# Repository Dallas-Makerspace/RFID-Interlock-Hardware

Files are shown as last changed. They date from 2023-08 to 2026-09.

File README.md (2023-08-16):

# RFID-Interlock-Hardware
Documentation and CAD source files for DMS RFID Interlock hardware

This is somewhat fragmentary documentation on the legacy RFID interlock box hardware (not those used in the woodshop) and a new version mechanically based on industry standard DIN rail components. 

Legacy hardware docs are divided into Legacy A - the prototype demo design used on the autolift and Shark lathe, and Legacy B - a group of unit constructed with parts on hand and slight mechanical variation.

Available CAD drawings only support complex parts.   I'll try and fill in some assembly drawings, possibly scans of hand drawings.

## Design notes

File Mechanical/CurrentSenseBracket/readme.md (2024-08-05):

3D printed and bent sheet metal versions of the current sense switch files.

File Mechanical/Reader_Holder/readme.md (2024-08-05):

RFID Reader holder 3D model and 3D print files

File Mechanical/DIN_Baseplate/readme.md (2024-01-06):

Template pattern for DIN baseplate and RIB current sense switch mounting bracket

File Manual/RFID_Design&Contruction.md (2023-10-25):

Dallas Makerspace RFID Lockout Design and Construction

# 1 Design

## 1.1 Avoided custom board design.

This is a no-production-volume design that will built in small quantites over years. Custom board designs were avoided because:

- They will become obsolete and unsupportable rapidly if extreme care is not taken in component selection, and likely even if that care is taken.
- The size and cost advantage is not great in the small number of large machine applications we have.

## 1.2 Readily Available Commodity Parts

The industrial parts used in this design and more expensive that their board level counterparts, but have longer market lives and available from several sources.

# 2 Fabrication and Construction

## 2.1 Waterjet Cutting Connector Hole

The inside of the box needs to protected from the jet. Even though the jet is scattered, it still contains enough energy to damage the internal powder coat. The rear and sidewall opposite the hinge need to be masked or protected in some way.

We've not tested an approach, but duct tape or an acrylic shield to protect the interior finish may work.

# 3 Versions

At this time there are _roughly_ three versions of Interlock. These are (informally) known as Legacy A, Legacy B, and DIN rail based designs.

The Legacy designs use an Eaton contactor with exposed electrical connections and have a protected high voltage compartment with a plastic cover that protects users from any voltage over 24 VAC.

Legacy A versions have the 5 VDC power supply mounted under the input side of the contactor. Only two seem to exist, one on the Shark Lathe in the Machine Shop and one on the Auto Lift. There are rumors of others.

Four Legacy B versions have been built and will likely end up on the Machine Shop milling machines, the Clausing lathe, and the Kalamazoo cold saw. The main apparent difference of this version is that the 5VDC power supply is mounted on the HV compartment wall.

The schematics of the two versions are similar, but not identical. The two legacy A variants are different as well. The Auto Lift unit has an RGB indicator mounted on it's top.

The DIN rail versions are based on a DIN rail mounted on 9.75" square plate.

# 4 Issues

## 4.1 Ethernet connection

Some Raspberry Pi Ethernet interfaces will not connect to some switches. This happens infrequently and can be resolved by connecting to a different brand or model switch. The cause of this issue has not been researched.

# 5 RFID Reader Identification

There are challenges identifying the RFID reader as the identification reported can vary a lot. Most readers do not seem to include a unique serial number. My hope was that future versions could use more than one reader to control multiple clients, unfortunately connecting multiple identical readers to a Raspberry PI only shows one reader. More study is needed. 

One solution was hoped to be to control reader identification by physical port. This is practical utilizing UDEV rules, but depends on underlying hardware. Raspberry Pi hardware versions may be determined by reading /proc/cpuinfo | Revision

[https://ozzmaker.com/check-raspberry-software-hardware-version-command-line/](https://ozzmaker.com/check-raspberry-software-hardware-version-command-line/)

**Table 1 Raspberry Pi Revision Codes**

| **Model and Pi Revision** | **RAM** | **Hardware Revision Code**** from cpuinfo** |
| --- | --- | --- |
| Model B Revision 1.0 | 256MB | 0002 |
| Model B Revision 1.0 + ECN0001 (no fuses, D14 removed) | 256MB | 0003 |
| Model B Revision 2.0
 Mounting holes | 256MB | 0004
 0005
 0006 |
| Model A
 Mounting holes | 256MB | 0007
 0008
 0009 |
| Model B Revision 2.0
 Mounting holes | 512MB | 000d
 000e
 000f |
| Model B+ | 512MB | 0010 |
| Compute Module | 512MB | 0011 |
| Model A+ | 256MB | 0012 |
| Pi 2 Model B | 1GB | a01041 (Sony, UK)
 a21041 (Embest, China) |
| PiZero | 512MB | 900092(no camera connector)
 900093(camera connector) |
| Pi 3 Model B Rev 1.2 | 1GB | a02082 (Sony, UK)
 a22082 (Embest, China) |
| Pi 3 Model B Plus Rev 1.3 | 1GB | a020d3 |
| PiZero W | 512MB | 9000c1 |
| Raspberry Pi 4 Model B Rev 1.1 | 4GB | c03111 |
|
| |
|
| |
| Data from several online sources and direct collection on devices in hand. |

We will need to add a udev rule that assigns reader(s) to port(s) and does so coarse verification of the connected device in an attempt to insure it's a reader.

Port identification and specification

[https://unix.stackexchange.com/questions/66901/how-to-bind-usb-device-under-a-static-name](https://unix.stackexchange.com/questions/66901/how-to-bind-usb-device-under-a-static-name)

udevadm info --attribute-walk /dev/ttyACM0

you get a screed of output but the salient bits are

KERNEL="video0", SUBSYSTEM="video4linux" and KERNELS="1:1.2.4:1.0".

# 6 RFID Reader I/O Assignment

We need to reliably locate the USB RFID reader. The commodity USB RFID readers are mostly based on the Sycreader chipset by RFID Technology Co., Ltd. The problem is that most are not serialized, and offer many different ID strings.

We also need to differentiate between readers in multi-contactor cases. The main advantage of multi-contactor installations is space savings as the cost savings are small.

Facing the the board edge, Pi 2 and 3 the Ethernet connection is on the left and the USB connections are on the right. The Pi 4 is a mirror image with USB ports in the center column.

Shape1 Shape2 Shape3

RFID reader connections are outlined in red. Pi 4 USB 3.0 connections are shaded in blue.

To retain the top USB slots for other purposes, the bottom USB slots are used on Pi 2 and 3 devices.

On the Pi 4 one column of USB connections is version 2.0, and the other is version 3.0. Facing the Pi 4 board edge, the ethernet connector is on the right, the USB 2.0 connections are on the left (outlined in red) and the USB 3.0 connections (highlighted in blue) are in the middle. On a Pi 4 we will use the USB 2.0 connections for the reader to preserve the USB 3.0 connections for other use.

Regardless, we want to assign card readers device names RFIDx where x is 0-9

We will accomplish this with a udev rules file.

The file must be in the /etc/udev/rules.d directory and should be named "10-local.rules" 

The rules file is maintained on the DMS KeyMaster GitHub.

## 6.1 [How to bind USB device under a static name?](https://unix.stackexchange.com/questions/66901/how-to-bind-usb-device-under-a-static-name)

https://unix.stackexchange.com/questions/66901/how-to-bind-usb-device-under-a-static-name

### 6.1.1 Writing udev rules

[http://www.reactivated.net/writing\_udev\_rules.html](http://www.reactivated.net/writing_udev_rules.html)

udevadm info --attribute-walk /dev/ttyAMA0

finding card reader mounts

ls /dev/input/by-path

# 7 Auto restart scripts

A bug in early code versions caused reads of unauthorized tags to crash the software. An expedient work around was used in the form of a bash script that checked for the presence of the process every second. If the process was not active, it would restart KeyMaster. While this is no longer necessary, it's a useful tool in the event of emergent problems like power blips. The original script did not do useful logging, all that happened was that the restart of keymaster generated a private local log. We are in the process of converting all logging to syslog.

Bash scripts can use syslog with the 'logger' command

logger _Some message to write_

There are several options available, including:

-i Log the process ID in each line

-f Log the contents of a specified file

-n Write to the specified remote syslog server

-p Specify a priority

-t Tag the line with a specified tag

See man 1 logger for more information on the tool.

# 8 Alternate AD lookups

Joshua Freedman wrote a new/much simpler AD lookup

https://discord.com/channels/862552330322182165/862555939159539732/1128763838230175744

adm\_d4rkfly3r@prlxjump02:~$ curl -X GET \

-H "Content-type: application/json" \

-H "Accept: application/json" \

-d '{"username":"d4rkfly3r","group":"3D Printer Basics"}' \

"192.168.203.30:8083/usernameGroupMembership"

{"inGroup":true,"activeMember":true}

Or

curl -X GET \

-H "Content-type: application/json" \

-H "Accept: application/json" \

-d '{"badge":"XXXXXXXXXX","group":"Machine Shop Shark Lathe"}' \

"192.168.203.30:8083/badgeGroupMembership"

| **DO NOT copy and paste text directly from this document.**** Word inserts non-printing characters that are not reliably stripped.** |
| --- |

How to use with keyfob #/AUTH GROUP Looks pretty straightforward:

[https://github.com/Dallas-Makerspace/CommonApi/tree/master](https://github.com/Dallas-Makerspace/CommonApi/tree/master)

**Badge in group check**

GET /badgeGroupMembership

Content-Type: application/json

{

"badge": "",

"group": "",

"breakCache": "false"

}

breakCache is optional, and likely should always be left the default false. It is only being left in for debugging purposes. Which will return 200 OK or 417 Expectation failed (when an invalid ldap precondition fails). A 200 OK Body will have a result like below:

# 9 Dust Collector Blast Gate Controls

The blast gates look pretty simple overall, the basically turn into a contact closure. This is true either literally, as in the case of the iVac consumer units, or as a switched AC voltage in the case of more industrial units.

RackMultipart20231024-1-vs8l2p.docx Page 8 of 8[Publish Date]

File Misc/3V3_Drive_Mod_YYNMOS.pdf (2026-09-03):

3/22/2026 | YYNOS 3.3V Drive Mod | OZINDFW

These boards normally require 6 or more volts of drive. The issue is that the optocoupler LED is in series with an LED and a current limiting resistor. The optocoupler voltage drop is about 1.7V at 20 mA. Since the indicator LED is also more than 1.5V, 3.3V drive will not work. The 470 Ohm current limiting resistor would limit drive to the optocoupler to only about 3 mA which is not enough drive for reliable operation.

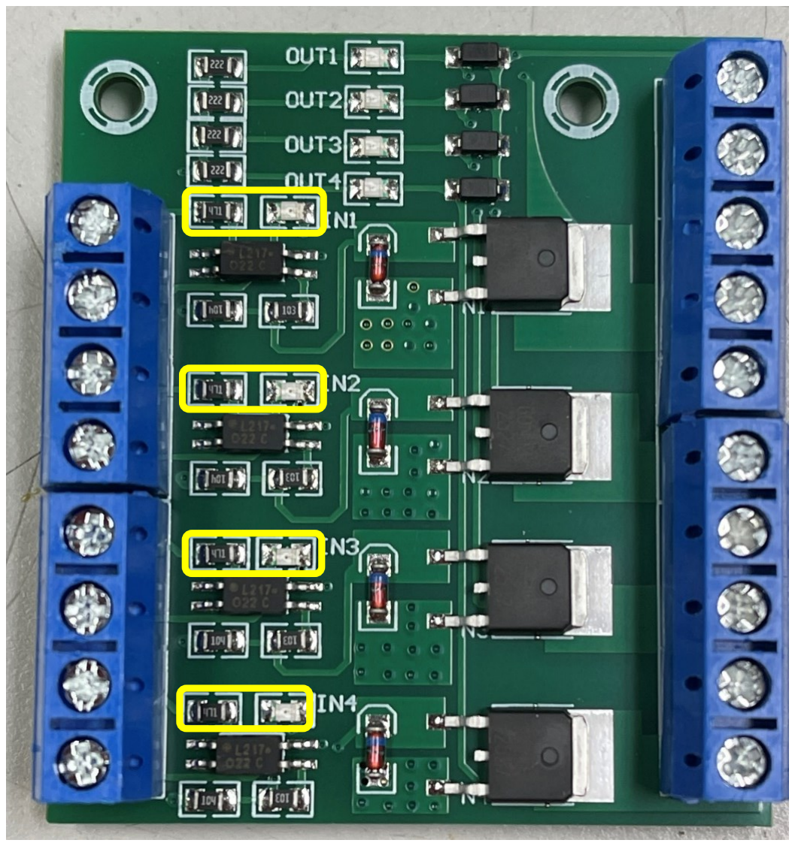
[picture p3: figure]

Figure 1 Unmodified YYNMOS-4

The modification involves removing the LED and replacing it with a short, and replacing the current limiting resistor with a lower value. I used 120 ohms which results in about 15 mA of drive – more than enough.

In Figure 2 I used a 120 ohm 0805 size surface mount resistor and a solder blob short. I didn’t have any zero ohm resistors of the correct physical size. I could have used two resistors that added up to the appropriate value, but I had the 120s on hand.

3/22/2026 | YYNOS 3.3V Drive Mod | OZINDFW

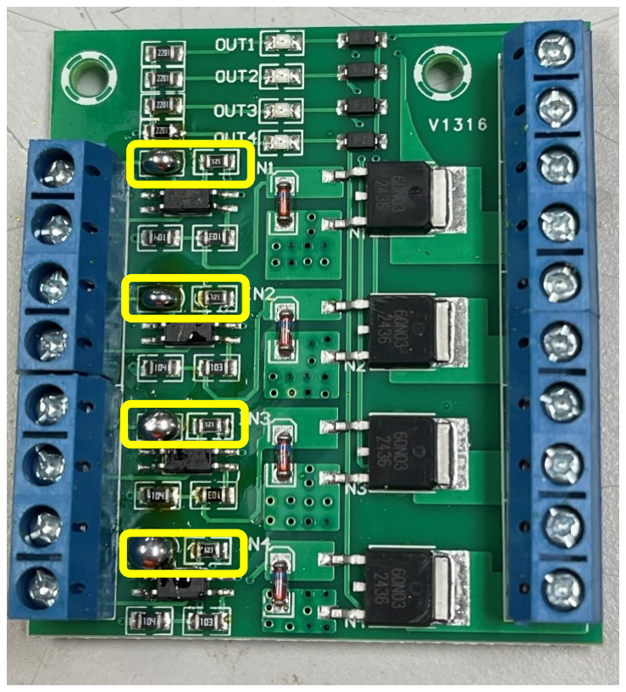
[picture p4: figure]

Figure 2 Modified YYNMOS-4

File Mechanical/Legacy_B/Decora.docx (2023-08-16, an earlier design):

Yes, all "Decora" style devices share the same cover plate opening, within a couple of thousandths of an inch (+/-.005" or so). GFCI receptacles also fit this description, as well as many dimmers, timers and "smart switches".

For instance the opening on a Hubbell plate is 1.312"x2.625" (http://www.hubbellcatalog.com/canada/catalogpages/section-c.pdf), while these Leviton are slightly different, but all within a reasonable spec to be called the same.

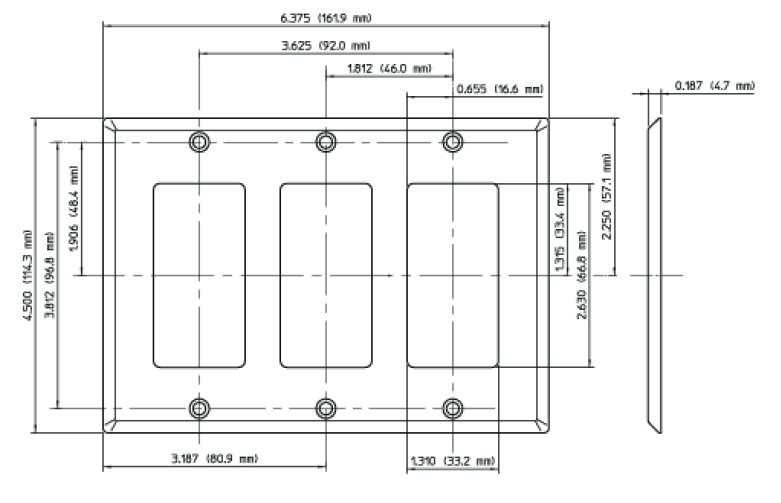
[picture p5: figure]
3 gang Decora cover plate drawing

W: 1.310 (min)

L: 2.630 (min)

R: 0.094 (0.079 347V)

C: 3.812 (4.062 347V) +/- 0.010 (counter-sunk for #6-32 UNC oval head machine screw)

Application (Face of device): 1.300 (max) W x 2.620 (max) L

page iv (https://www.nema.org/Standards/view/Wiring-Devices-Dimensional-Specifications) notes: (#1) dimensions are in inches (#2) tolerances are +/- 0.005 (#10) dimensions are for interchangeability and do not preclude other designs.

NEMA WD 6-2016 (https://www.nema.org/Standards/view/Wiring-Devices-Dimensional-Specifications), page 5 says:

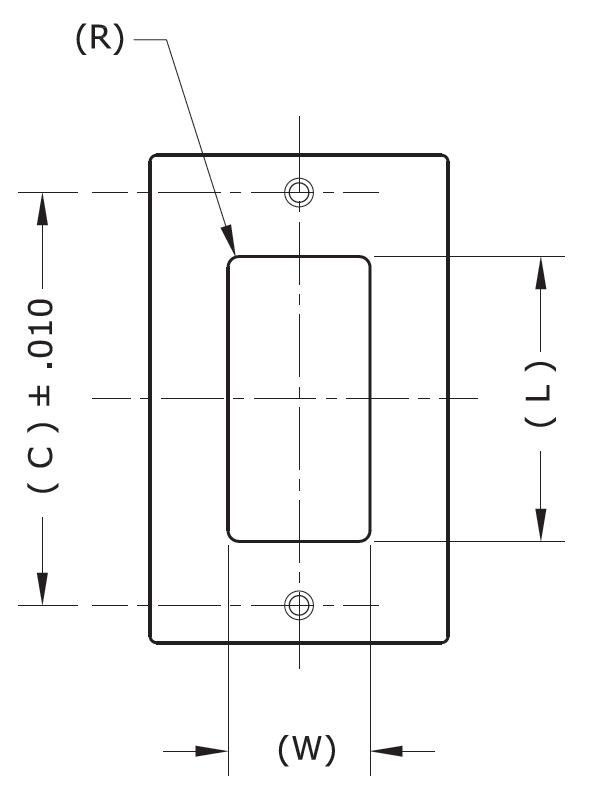
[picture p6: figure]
Wallplate Dimensions for Rectangular Face Devices

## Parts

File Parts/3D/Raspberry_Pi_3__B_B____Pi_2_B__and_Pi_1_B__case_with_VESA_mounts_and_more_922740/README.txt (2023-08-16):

Raspberry Pi 3 (B/B+), Pi 2 B, and Pi 1 B+ case with VESA mounts and more by 0110-M-P on Thingiverse: https://www.thingiverse.com/thing:922740

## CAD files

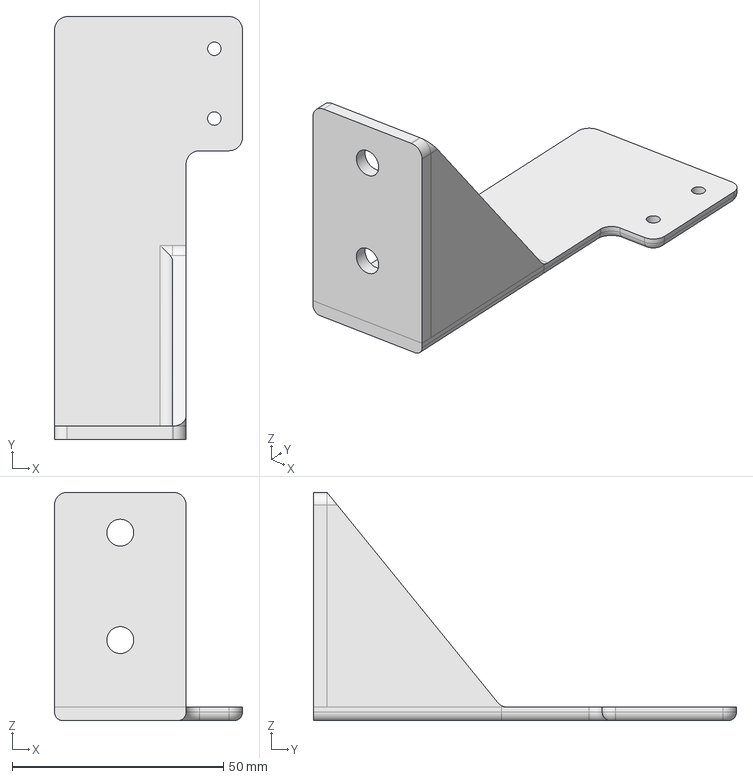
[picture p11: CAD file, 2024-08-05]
Mechanical/CurrentSenseBracket/RFID_CurrentSense_Bracket_3D_0v1d.FCStd
44.5 x 100.0 x 54.0 mm

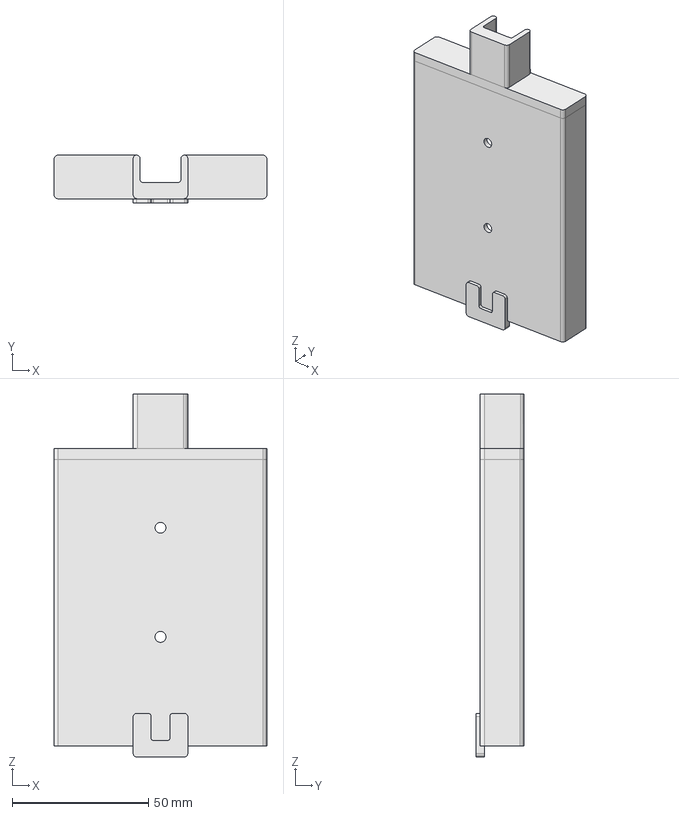
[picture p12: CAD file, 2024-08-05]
Mechanical/Reader_Holder/Reader_Holder_0v6a.FCStd
78.0 x 17.5 x 133.0 mm

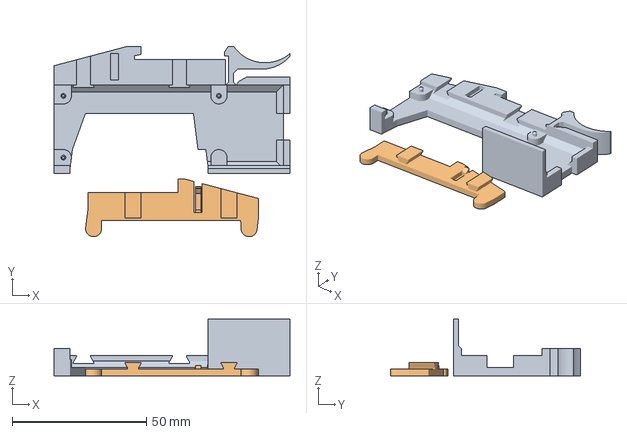
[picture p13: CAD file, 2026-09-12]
Mechanical/RPi_Zero_DIN_Mount/rpi_zero_din_rail.3mf
88.0 x 71.0 x 21.1 mm
rpi_zero_din_rail.stl
stopper.stl

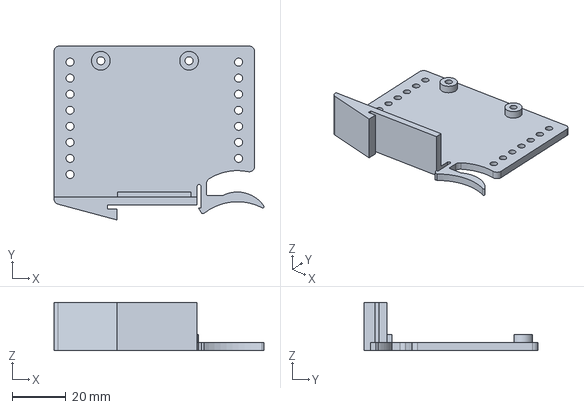
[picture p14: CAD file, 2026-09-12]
Mechanical/YYNMOS-4_MOSFET_Sw_Bracket/YYNMOS4_DIN_0v4.FCStd
78.5 x 65.0 x 18.0 mm

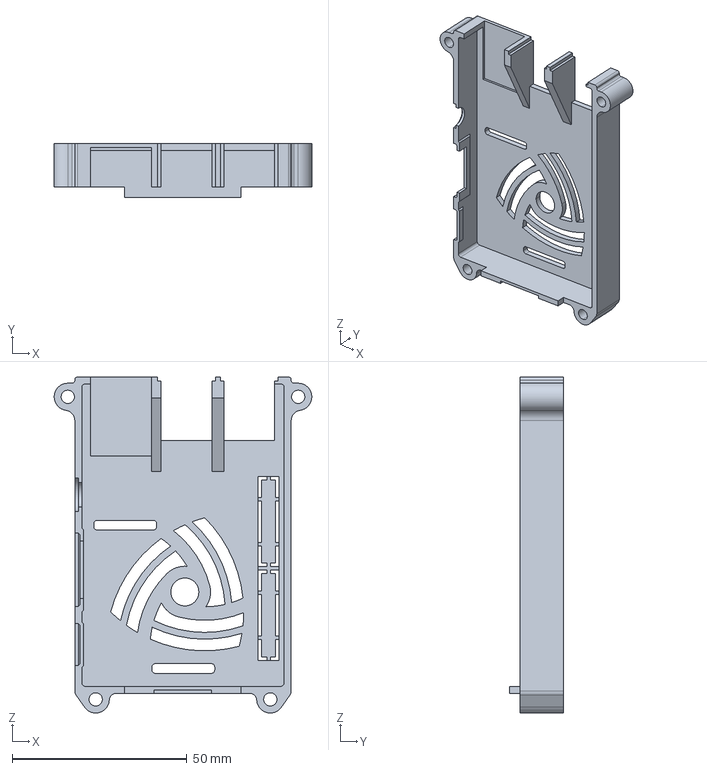
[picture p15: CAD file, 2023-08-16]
Parts/3D/Raspberry_Pi_3__B_B____Pi_2_B__and_Pi_1_B__case_with_VESA_mounts_and_more_922740/files/rpi2-top.stp
73.8 x 15.5 x 96.2 mm

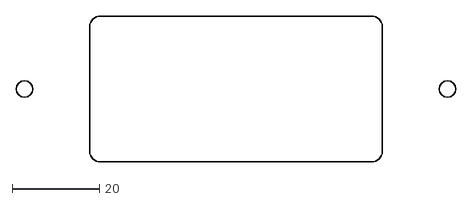
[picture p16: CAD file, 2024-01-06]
Mechanical/KeystoneCutout/KeystoneCutout0v1b.dxf
100.6 x 33.4

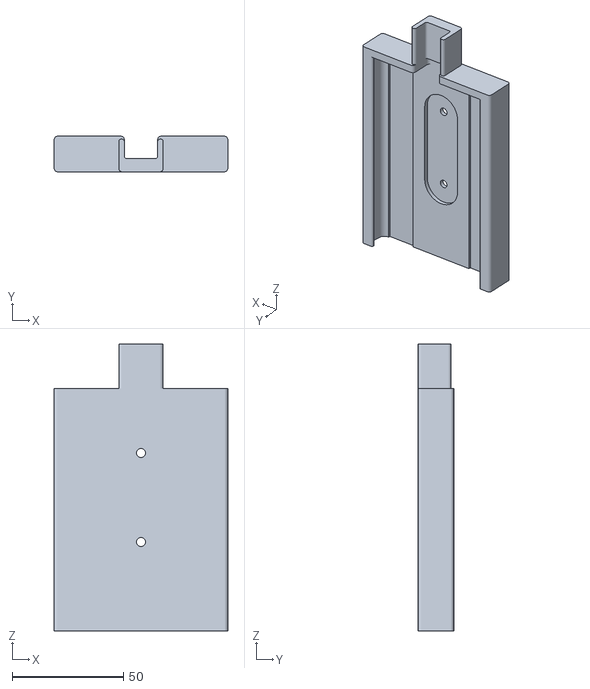
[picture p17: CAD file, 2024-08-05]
Mechanical/Reader_Holder/Reader_Holder_0v6a-Body.stl
78.0 x 16.0 x 129.0

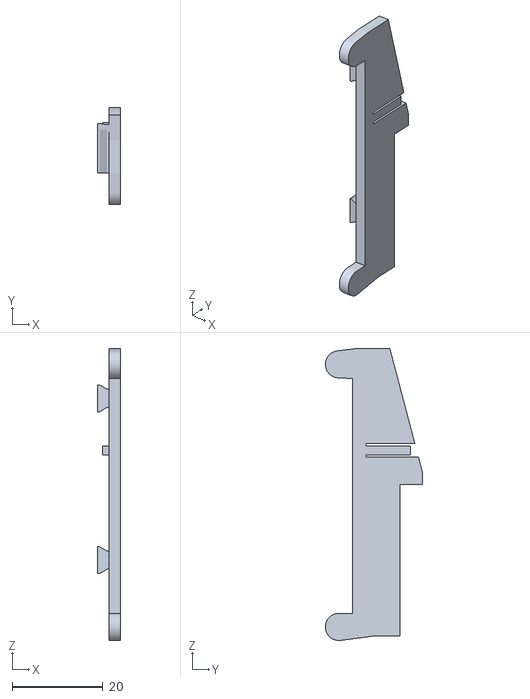
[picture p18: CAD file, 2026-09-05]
Mechanical/RPi_Zero_DIN_Mount/stopper.stl
5.01 x 21.5 x 64.5

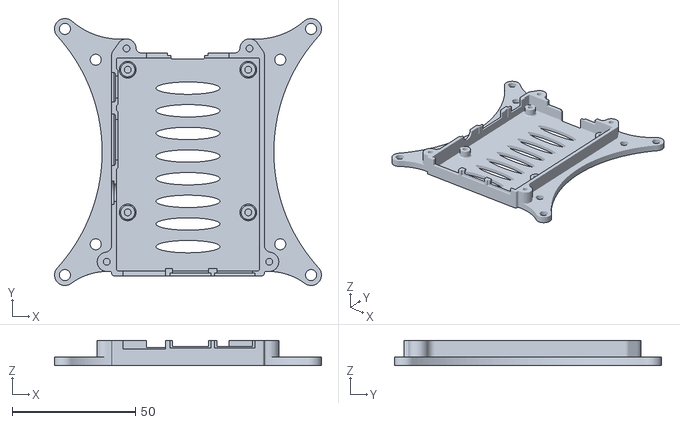
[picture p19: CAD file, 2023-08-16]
Parts/3D/Raspberry_Pi_3__B_B____Pi_2_B__and_Pi_1_B__case_with_VESA_mounts_and_more_922740/files/rpi3-bottom_100mm-vesa_netfabb.stl
108.5 x 108.5 x 10.3

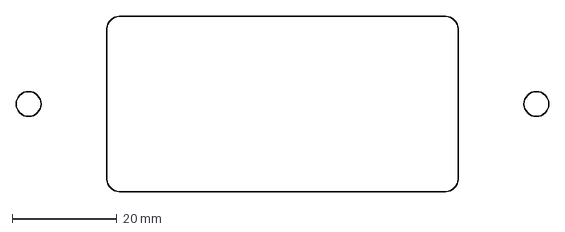
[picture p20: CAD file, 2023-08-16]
Mechanical/KeystoneCutout/KeystoneCutout0v1a.dxf
101.6 x 33.4 mm

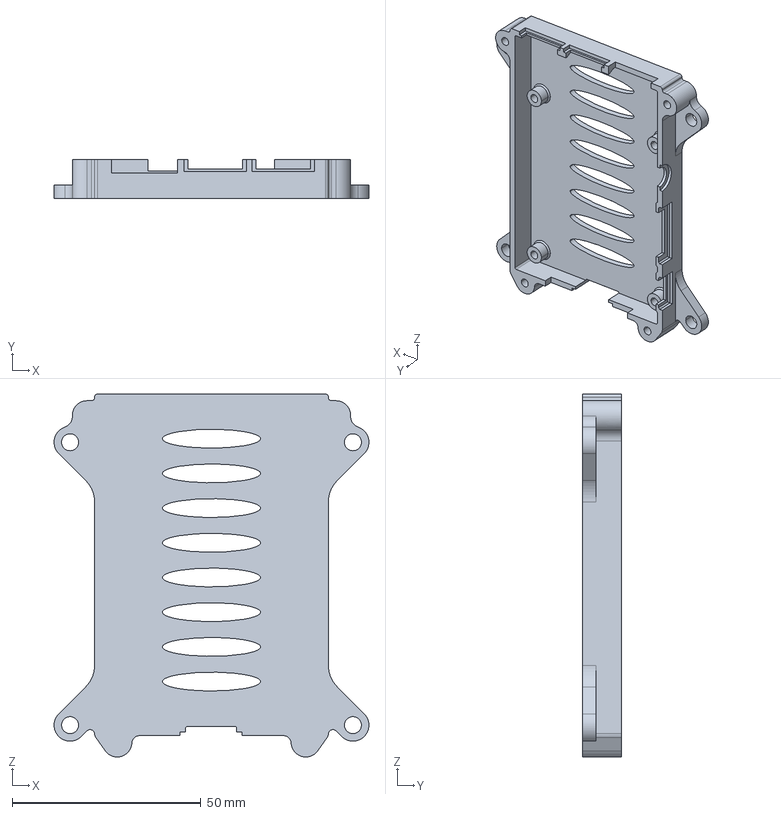
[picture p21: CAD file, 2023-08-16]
Parts/3D/Raspberry_Pi_3__B_B____Pi_2_B__and_Pi_1_B__case_with_VESA_mounts_and_more_922740/files/rpi3-bottom.stp
83.5 x 10.3 x 96.2 mm

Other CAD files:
Mechanical/DIN_Baseplate/RFID_CurrentSense_Bracket_3D_0v1b-Body.stl
Mechanical/KeystoneCutout/KeystoneCutout0v1.FCStd
Mechanical/CurrentSenseBracket/RFID_CurrentSense_Bracket_3D_0v1d-Body.stl
Mechanical/DIN_Baseplate/RFID_CurrentSense_Bracket_3D_0v1b.FCStd
Mechanical/YYNMOS-4_MOSFET_Sw_Bracket/YYNMOS4_DIN_0v3-Case.step
Mechanical/CurrentSenseBracket/RFID_CurrentSense_Bracket_3D_0v1d-BodyFillet.stl
Mechanical/DIN_Baseplate/RFID_CurrentSense_Bracket_Dim_0v2.FCStd
Mechanical/CurrentSenseBracket/RFID_CurrentSense_Bracket_0v2.DXF
Mechanical/CurrentSenseBracket/RFID_CurrentSense_Bracket_0v2.FCStd
Mechanical/CurrentSenseBracket/RFID_CurrentSense_Bracket_sheet_Metal_0v1b.FCStd
Mechanical/DIN_Baseplate/RFID_CurrentSense_Bracket_Bare_0v2.FCStd
Mechanical/DIN_Baseplate/RFID_LO_DIN_Baseplate_0v2b.FCStd
Mechanical/DIN_Baseplate/RFID_LO_DIN_Baseplate_0v2b.dxf
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

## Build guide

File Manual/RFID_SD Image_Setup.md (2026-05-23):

Dallas Makerspace Legacy RFID Lockout SD Card Setup

# 1 Create New SD Card image

## 1.1 Obtain Raspberry Pi OS Image File

Download or otherwise obtain a copy of the latest Raspberry Pi OS (was called Raspbian.) Select the lightest 32-bit version available (no desktop, etc.)

[https://www.raspberrypi.com/software/](https://www.raspberrypi.com/software/)

## 1.2 Card Selection

The best option appears to be "high endurance" SD cards of 8 GB or greater.
These are usually made for security video and other high write duty cycle applications.
 
## 1.3 Raspberry Pi OS Installation

Using the SD card imager of your choice, or the Raspberry Pi foundation Raspberry Pi Imager, install an image on

You can get an image from the Raspberry Pi site that includes a Raspberry pi OS installer, but these have historically been limited to the (large) desktop version.

### 1.3.1 balenaEtcher

Available for Windows, MacOS, and Linux, this is a simple and very effective application.

https://balenaetcher.org/

### 1.3.2 Win32DiskImager

| **Caution!**** There are several sites that purport offer Win32DiskImager downloads that add malware.** |
| --- |

The correct 'official' site is:

[https://sourceforge.net/projects/win32diskimager/files/latest/download](https://sourceforge.net/projects/win32diskimager/files/latest/download)

## 1.4 Network Configuration

Need to modify network manager settings, so edit:

_/etc/dhcpcd.conf_

And set the appropriate static address

Note: Using Network Manager leads to host of issues that make copying the card image a mess. Network Manager includes the ethernet interface mac address in a GUID used a number of places, not all of which appear to be documented.

### 1.4.1 WiFi Configuration

If the applicaiton uses WiFi use the command:

_sudo nmtui_

to configure WiFi and IP settings with the appropriate static address. Some versions of Raspberry Pi OS need options disabled to maintain a reliable connection. If you observe frequent data drops try:

Create a file called /etc/modprobe.d/brcmfmac.conf

 with the following content:

_options brcmfmac roamoff=1 feature_disable=0x82000_

Reference: https://forums.raspberrypi.com/viewtopic.php?t=372254

### 1.4.2  SSHD Configuration

***Note that this step appears to not be needed and breaks Trixie based versions***

The OpenSSH daemon has added QoS metric requirements that the Pi Zero W Wifi can't meet. This results in dropped SSH/SFTP sessions, often before login completes. Edit 

_/etc/ssh/sshd_config_

and add the line

_IPQoS 0x00_

Refernce: https://raspberrypi.stackexchange.com/questions/143142/has-anyone-solved-raspberry-pi-zero-w-ssh-client-loop-send-disconnect-broken

## 1.5 Raspberry Pi OS Configuration

On first boot you will be asked for a language, username and password. Use:

- Select US English
- Username keymaster,
- Password dmsDMS

Run:

**sudo raspi-config**

- Update raspi-config tool to latest version. If you just downloaded the OS, it is likely the tool is the latest version, but this is not guaranteed.

## 1.5 Make raspi-config changes:

*Note that later versions of raspi-config renumber options.*

### 1.5.1 System Options

- 1 System|S4 Hostname Interlock-Test-1
- S5 Boot/Autologin|B2 Console Autologin
- S6 Network at boot (do not wait for network)
- S8 Power LED – change to indicates power if option is available

### 1.5.2 Display Options (none)

### 1.5.3 Interface Options

- I2 SSH (Enable)
- I4 SPI (enable) if PiFace is used (Legacy only)

### 1.5.4 Localization

- L1 Locale EN\_US.UTF-8 (disable EN\_GB if selected) and set en\_US as default
- L2 Timezone America/Chicago
- L3 Keyboard Generic 104-Key/US default layout no compose key
- L4 WLAN Country US (United States)

### 1.5.5 Advanced Options

- A4 Network Interface Names (Disable predictable network I/F Names)
- AA Network Config|dhcpcd

**NOTE: If this image is intended to be copied to other cards, it's best to hold off on the following config until the final card it used.**

The A1 Expand Filesystem option expands the Pi OS image to fill the entire card. This will restrict the use of the image to cards larger than the image

- A1 Expand Filesystem – (hold till complete)

Finish and reboot

## 1.6 Remove avahi

Avahi generates mDNS traffic that adds no value in this application. To remove it:

sudo apt-get purge avahi-daemon

## 1.7 Install Python Libs

Before doing anything else update the OS

_sudo apt-get update_

install pip

_sudo apt-get install python3-pip_

_sudo pip install evdev_

later versions of Rapberry Pi OS 'externally manage' Pi libraries and require anything not upported by the OS to be installed in a virtual environment.  evdv *IS* supported so can be installed with APT:

_sudo apt install python3-evdev_

### 1.7.1 Configure Pi GPIO Support

In order to use the GPIO ports your user must be a member of the gpio group. 
The pi user is a member by default, other users need to be added manually. To add a user:

  sudo usermod -a -G gpio keymaster

### 1.7.2 Piface DigitalIO 2 Support

*PiFace is _ **only** _ used on legacy systems as the PiFace DigitalIO 2 cards are no longer available.*

_pip install pifacecommon_

_pip install pifacedigitalio_

## 1.9 Keymaster Install

Copy Python code and subdirectories into /home/Keymaster

Add and configure KeyMaster.ini file

## 1.8 Install UDEV Rules

Copy the latest version of the UDEV rules file to /etc/udev/rules.d directory. The file should be named "10-local.rules"

## 1.10 Bash Script Edits

The ".bashrc" needs some additions

Copy line(s) from aux\_files\bashrc-addendum.bash into the end of .bashrc

Copy file aux\_files\KeyMaster\_Start.sh to \home\keymaster and make executable with

_sudo chmod +x KeyMaster\_Start.sh_

## 1.12 Read Only Card Configuration

While we have examples of systems running cards with local logging to SD for years, Flash wearout is a well-documented issue. The best option seems to be to log to local RAMDISK and network logger.

Add instructions here.

[1](#sdfootnote1anc) While cards smaller than 8 GiB may fit an image, smaller cards don't really leave enough working room for flash wear leveling.

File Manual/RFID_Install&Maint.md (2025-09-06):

Dallas Makerspace Legacy RFID Lockout Installation and Maintenance
|

| **DO NOT configure for operation at input voltage greater than 240V.** If 480V operation is required, see Appendix A; Configuration for operation on 480 V (Untested) |
| --- |

# 1 Before You Begin

Note that the RFID Interlocks as currently built and tested have not been modified for power in/out ports, any indicators, or an Emergency Stop switch as these are installation dependent.  You will need to survey and plan the installation so that any required chassis modifications can be made prior to installation and commissioning. These instructions do not cover these modifications nor do they discuss mounting the interlock chassis/box.

## 1.1 Material Required

- Interlock hardware for configuration.
- Suitable micro SD card – minimum of 4 GiB, recommend 16 GiB or greater to provide lots of spare capacity for wear leveling.
- Box mounting material (wall anchors, etc.)
- Double sided mounting tape for reader installation.

## 1.2 Required Information

Have the following information at hand:

- Hostname
- Fixed IP address for unit (ping hostname while at DMS to obtain.)
- The Active Directory security group that controls the target device (these are continuously added to and changing, but one example is "Automotive 102 (Lift Training)" for the Automotive Committee car lift.
- The password for the device. Generating the password with and storing it in the DMS Bitwarden IoT folder before using it would be a good idea.
- Required operating voltage
- Phase count (single or three phase)
- Load current or horsepower rating

## 1.3 Tools/Facilities

Have access to:

- SSH/SFTP terminal
- Multimeter
- Test supply of required voltage
- DMS Ethernet port on VLAN 400 (the IoT VLAN)
- Very small screwdrivers required for current switch adjustment and DIN connection block screws
- 1/4" flat blade screwdriver and #1 Phillips screwdriver
- 3/8" socket or nutdriver for installing the baseplate retaining nuts.

# 2 Create and Configure SD card

Copy the latest image on to a micro SD or create one according to the instructions in the latest version of RFID\_LO\_SD\_IMAGE\_Setup

## 2.1 SD configuration

You can do this from the autologin console on the Pi or by SSH to the default image DNS of Interlock-Test-1 with the password dmsDMS. If you use SSH you will need a network connection on VLAN 400.

### 2.1.1 Resize Partition

Run the Raspberry Pi configuration utility and resize the partition to fill the card.

sudo raspi-config

select Advanced Options, and option A1 Expand Filesystem

### 2.1.2 Set hostname

Edit the /etc/hostname file:

sudo nano /etc/hostname

and enter the desired hostname. Edit the /etc/hosts

sudo nano /etc/hosts

file to change the localhost home alias entry (probably the last in the file) from:

127.0.0.1 Interlock-Test-1

To reflect the new hostname.

#### 2.1.2.1 Hostname Selection

Three elements separated by hyphens, all caps.

COMMITTEE-MACHINE-INDEX

**COMMITTEE** name - Wood, Machine, Metal, etc

**MACHINE** name – eg SAWSTOP for SawStop table saw, or COLCHESTER for Colchester lathe

**INDEX** – a sequential number starting with one and continuing with upper case letters if needed

So the woodshop's second SawStop would be WOOD-SAWSTOP-2

## 2.2 Password Setting

Set new passwords for the Keymaster User account in accordance with DMS password selection standards and enter it in Bitwarden in the IoT folder for the hostname.

## 2.3 Keymaster Configuration

Select AD name for authorization. 

Edit the [ADCommonAPIAuth] section of /home/KeyMaster/KeyMaster.ini

[ADCommonAPIAuth]

url = http://192.168.203.30:8083/badgeGroupMembership

group =

(where the authorization group follows the equal sign and is not in quotes)

~~Edit the [ADApiAuth] section of /home/KeyMaster/KeyMaster.ini~~

~~[ADApiAuth]~~

~~url = http://192.168.200.32:8080/api/v1/lookupByRfid~~

~~# Groups denied are checked first, then groups allowed are checked~~

~~groups\_denied =~~

~~groups\_allowed = Automotive 102 (Lift Training)~~

~~and replace the groups\_allowed entry with the AD for the system. groups\_denied should remain blank.~~

## 2.4 Network Configuration

It is probably best to leave this to the very last as interlocks at DMS use fixed IPs on a dedicated VLAN subnet. The VLAN is 400 and is determined by switch port configuration. The subnet is the RFC1918 non-routable, private range 10.0.0.0 0 - 10.255.255.255 (10/8 prefix)

The IoT IP range is not routable by the DMS user subnet.

~~Copy dhcpcd.conf from the aux-files/Network folder to /etc/dhcpcd.conf and edit the static IP address~~

Use Network Manager to configure the netowrk interface:

sudo nmtui

## 2.5 Labelling

- Apply High Voltage Caution label if not present
- Apply hostname label to cabinet (best to use top of cabinet so label is visible with door open
- Apply hostname label to baseplate

# 3 Installation

- Remove ground screw and four mounting nuts on baseplate (need pic) and remove the baseplate assembly.
- Select and remove cable entry and exit knockouts or cut holes for this purpose.
- Mount box/cabinet
- Route input and output cables
- Reinstall Baseplate
- Install (but do not tighten) ground screw.
- Place all corner nuts finger tight, then tighten them completely
- Tighten the ground screw

## 3.1 Wiring

### 3.1.1 Single Phase Application

In single phase applications the neutral should use the contactor middle terminals. The line (hot) should pass through the current sensor.

### 3.1.2 Three Phase Application

# 4 Test and Calibration

## 4.1 Current Sensor adjustment

Turn the machine in it's unloaded running state (with motor on, but unloaded.) Adjust current switch so light just comes on. Turn motor off and verify sensor light turns off.

# 5 Commissioning
- Create and initially populate controlling AD entry (if not already done - need at least one entry for testing.)
- Edit keymaster.ini with new AD (if not already done.)
- Update Password from default and generate Bitwarden entry for interlock.
- Delete existing logs (keymaster and console) to get rid of leagacy image and testing entries
- Reboot and check function.

# 6 Maintenance

Log checks

# Appendix A

# 7 Configuration For Operation On 480 V (Untested)

**NOTE THAT THIS CONFIGURITION IS UNTESTED AND ONLY APPLIES TO LEGACY STYLE INTERLOCKS**

The low voltage power supply input is rated for a maximum input operating voltage of 240 V. It should be possible to use the transformer input as an autoformer. Connect the power supply input between the common and 208V tap. Connect the 480 V input between the common and 480V tap.

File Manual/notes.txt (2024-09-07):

There may be power save issues that cause the wifi to dissappear (device and all)

See https://raspberrypi.stackexchange.com/questions/138688/wifi-disconnects-after-6-hours-on-raspian-11-pi-zero-2w

and   https://raspberrypi.stackexchange.com/questions/96606/make-iw-wlan0-set-power-save-off-permanent

So far I haven't been able to successfully disable it. Except that I have.  It's not clear if 

sudo systemctl disable wifi_powersave@on.service
sudo systemctl enable wifi_powersave@off.service

did this after

One way to accomplish this is to build a systemd unit file which can execute the necessary command at boot. I will give you here a bit more comfortable example for switching off or on power_save. Create a Unit file with:

rpi ~$ sudo systemctl --full --force edit wifi_powersave@.service

In the empty editor insert these statements, save them and quit the editor:

[Unit]
Description=Set WiFi power save %i
After=sys-subsystem-net-devices-wlan0.device

[Service]
Type=oneshot
RemainAfterExit=yes
ExecStart=/sbin/iw dev wlan0 set power_save %i

[Install]
WantedBy=sys-subsystem-net-devices-wlan0.device

editing /etc/rc.local did not seem to work on boot up

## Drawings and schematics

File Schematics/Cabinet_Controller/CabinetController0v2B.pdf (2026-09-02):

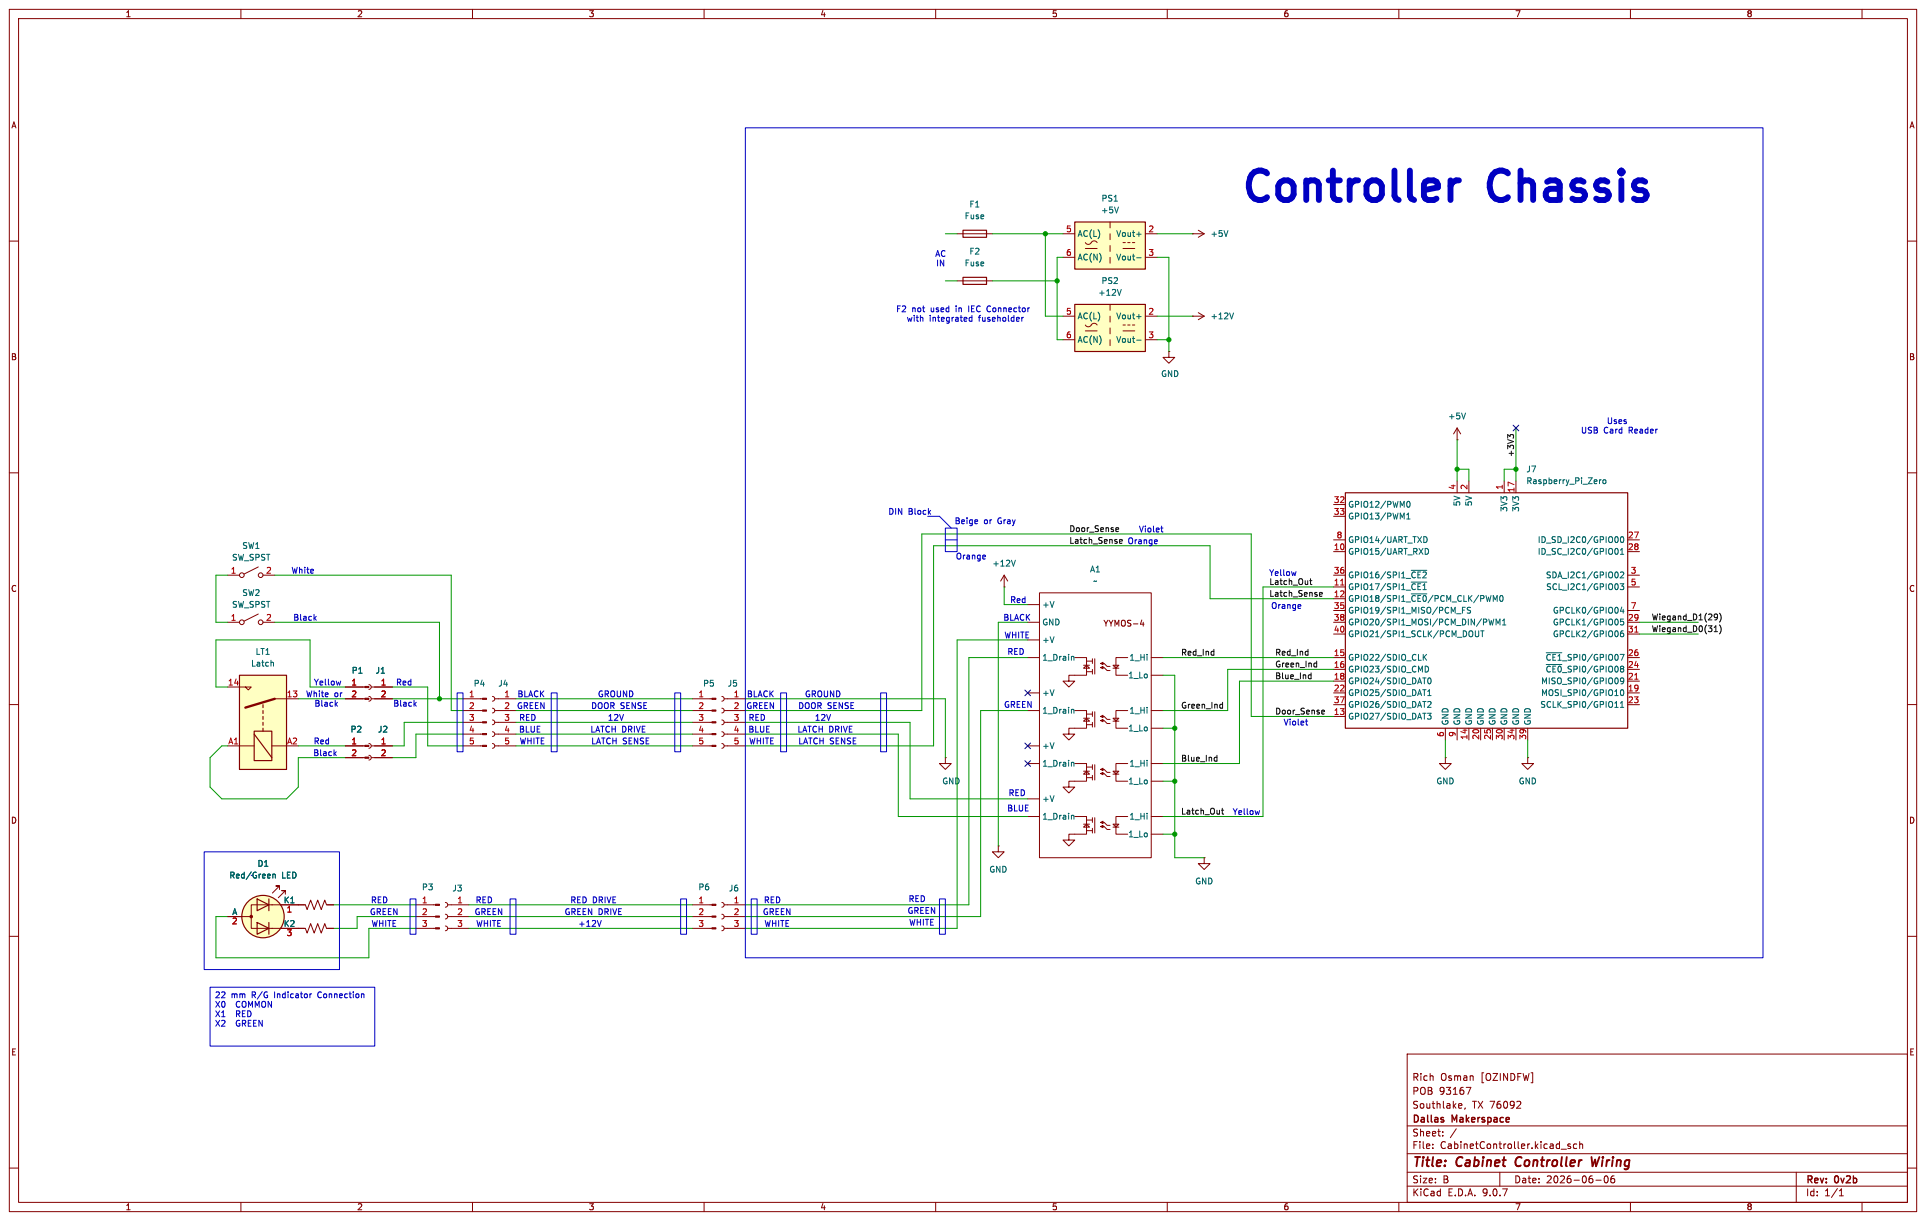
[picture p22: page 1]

Uses USB Card Reader Violet Red BLUE GREEN
1_Hi 1_Lo +VGND

Id: 1/1 Title: Cabinet Controller Wiring

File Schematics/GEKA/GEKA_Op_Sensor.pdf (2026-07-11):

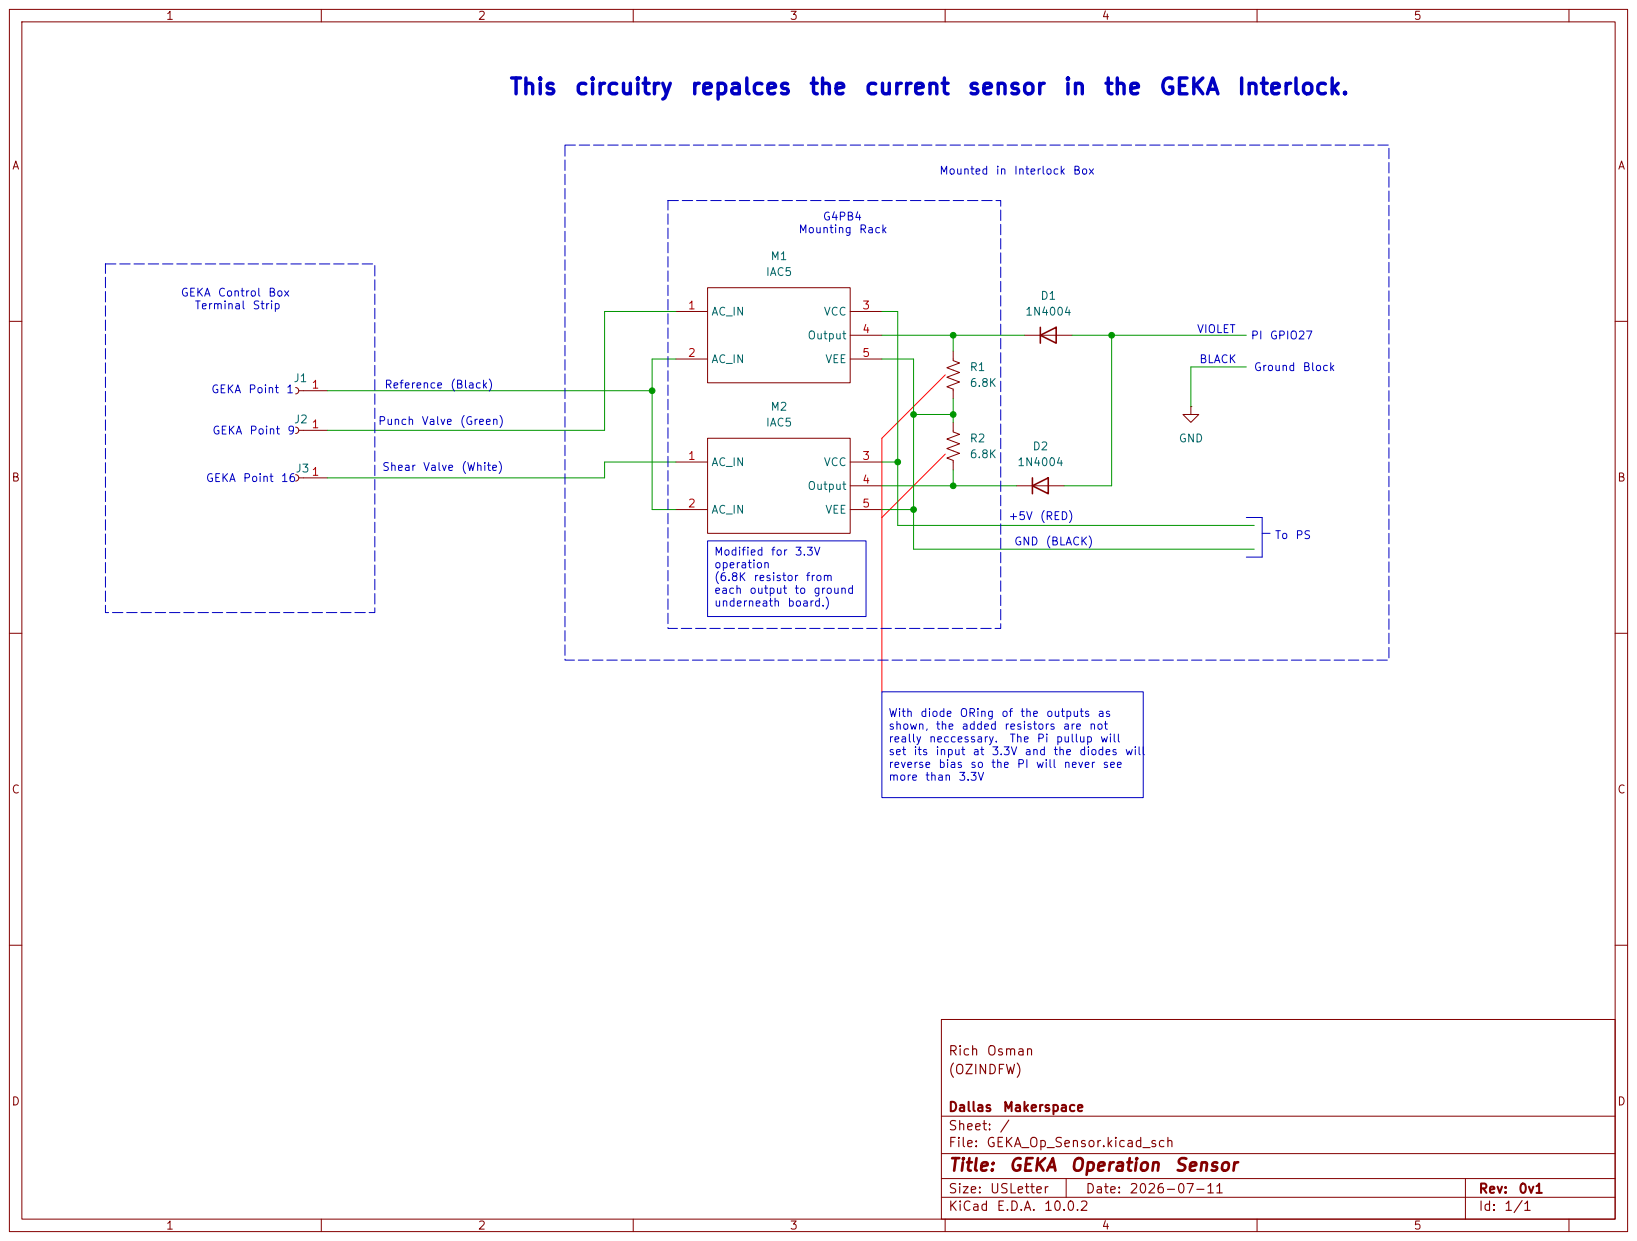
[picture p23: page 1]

This circuitry repalces the current sensor in the GEKA Interlock.

shown, the added resistors are not really neccessary. The Pi pullup will set its input at 3.3V and the diodes will reverse bias so the PI will never see more than 3.3V Modified for 3.3V operation

(6.8K resistor from
each output to ground

Dallas Makerspace
Sheet: /
File: GEKA_Op_Sensor.kicad_sch
Title: GEKA Operation Sensor

Size: USLetter | Rev: 0v1
KiCad E.D.A. 10.0.2 | Id: 1/1

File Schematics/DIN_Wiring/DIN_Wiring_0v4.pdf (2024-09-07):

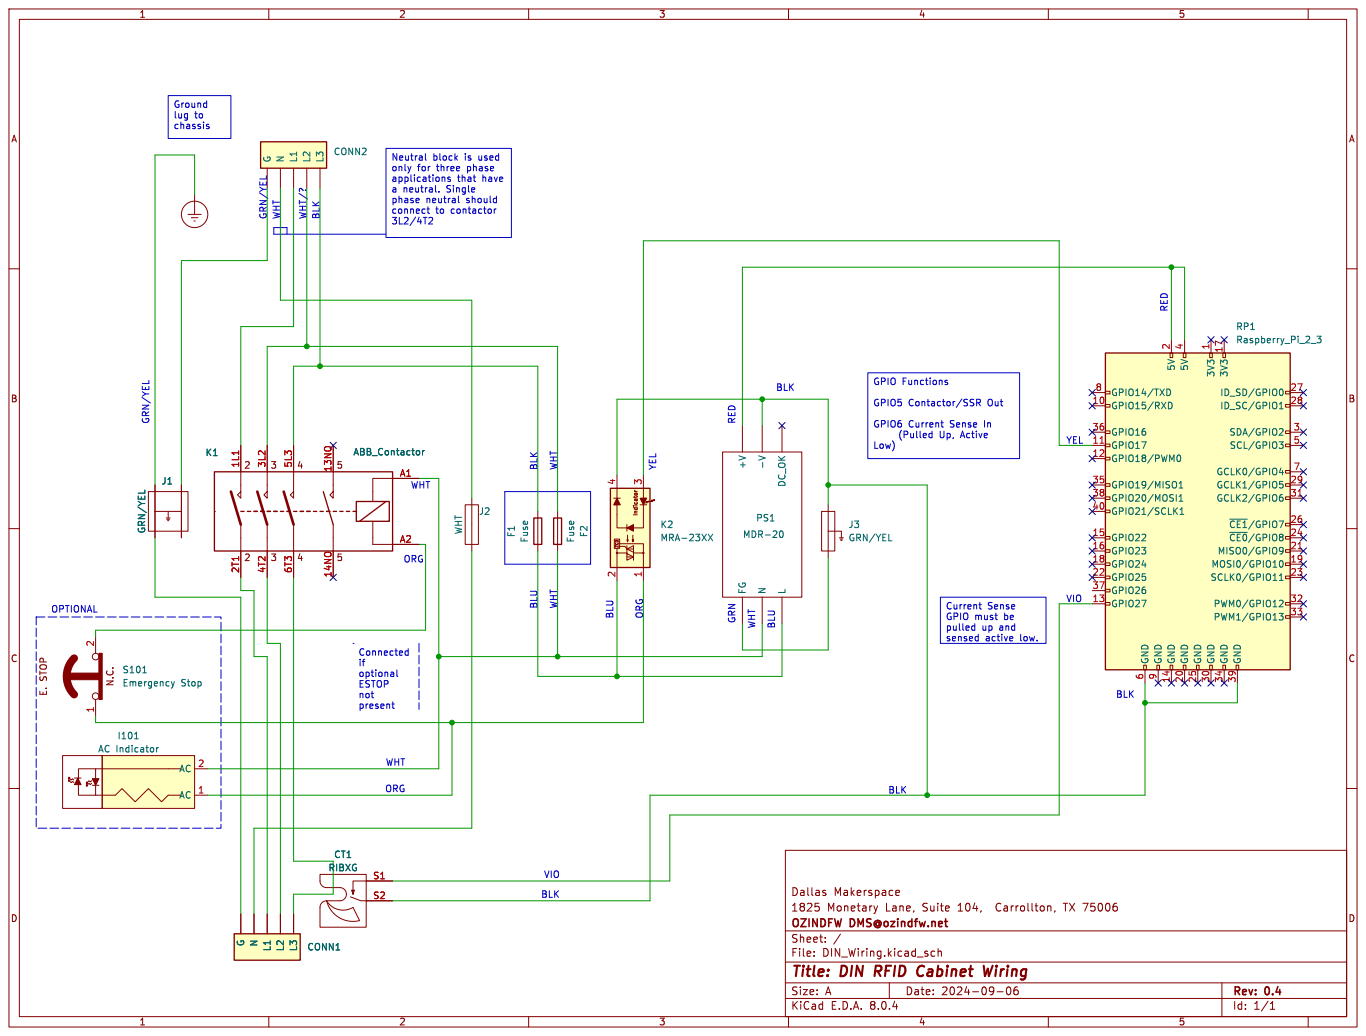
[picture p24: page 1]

Neutral block is used
only for three phase
phase neutral should

NL1L2L3CONN1 F2 Fuse YEL BLK BLU GRN/YEL OPTIONAL WHT VIO

Id: 1/1 Title: DIN RFID Cabinet Wiring

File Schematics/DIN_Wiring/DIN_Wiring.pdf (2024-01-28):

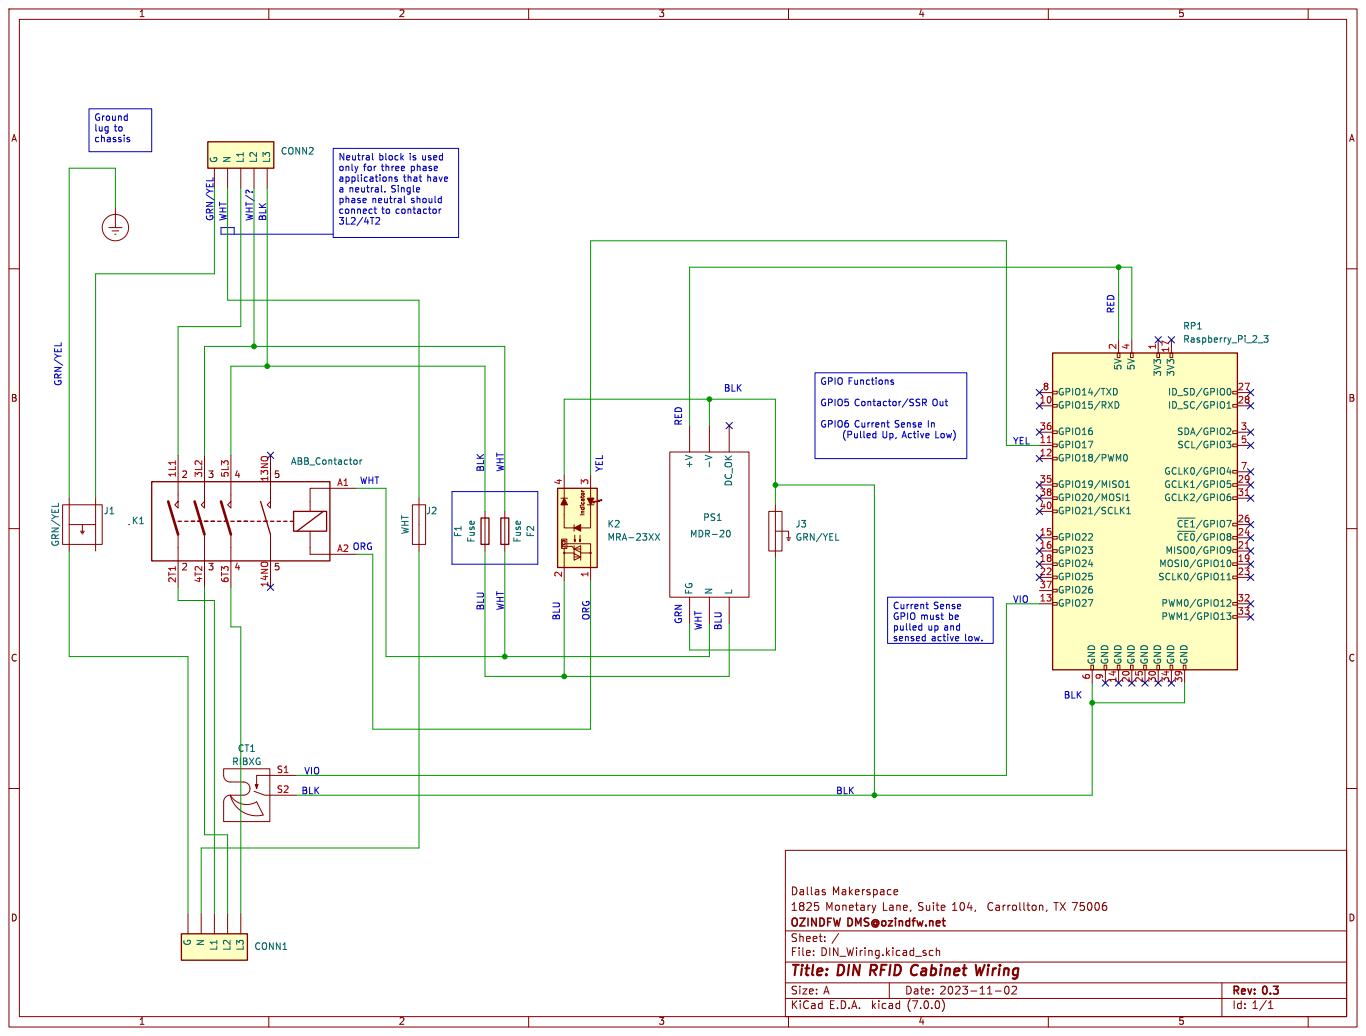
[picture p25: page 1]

only for three phase
a neutral. Single
phase neutral should

NL1L2L3CONN1 F2 FuseJ3GRN/YEL S1S2 CT1 RIBXG ZCD Indicator 2

Id: 1/1 Title: DIN RFID Cabinet Wiring

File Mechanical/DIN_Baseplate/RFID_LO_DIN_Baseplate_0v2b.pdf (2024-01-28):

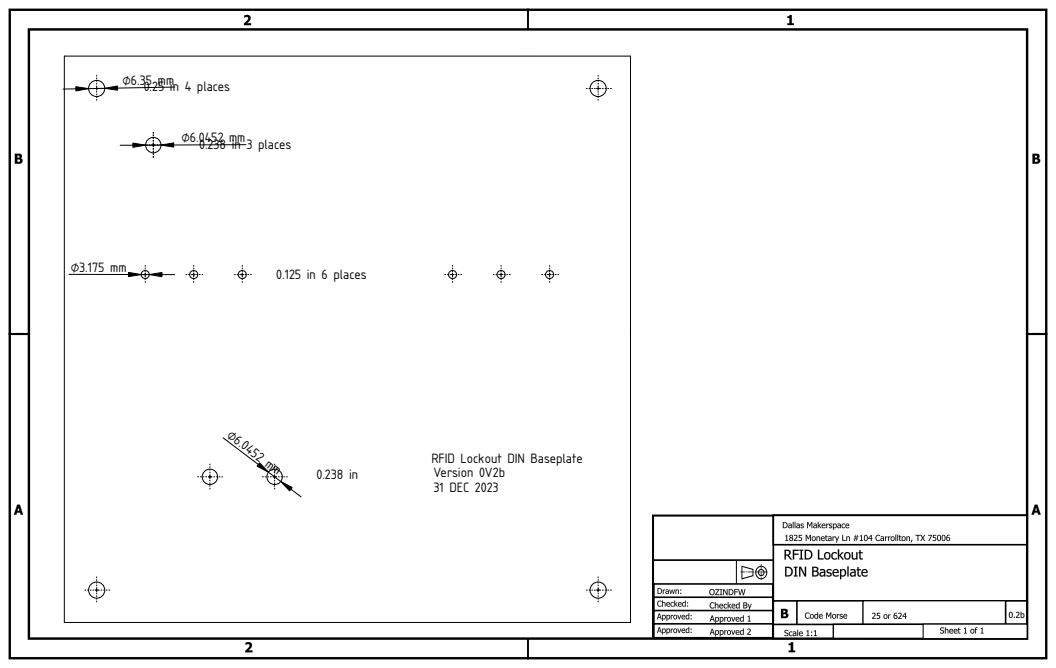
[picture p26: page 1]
⌀6.0452 mm 0.238 in 3 places; 0.25 in 4 places; 0.125 in 6 places; RFID Lockout DIN; Baseplate; Version 0V2b 31 DEC 2023

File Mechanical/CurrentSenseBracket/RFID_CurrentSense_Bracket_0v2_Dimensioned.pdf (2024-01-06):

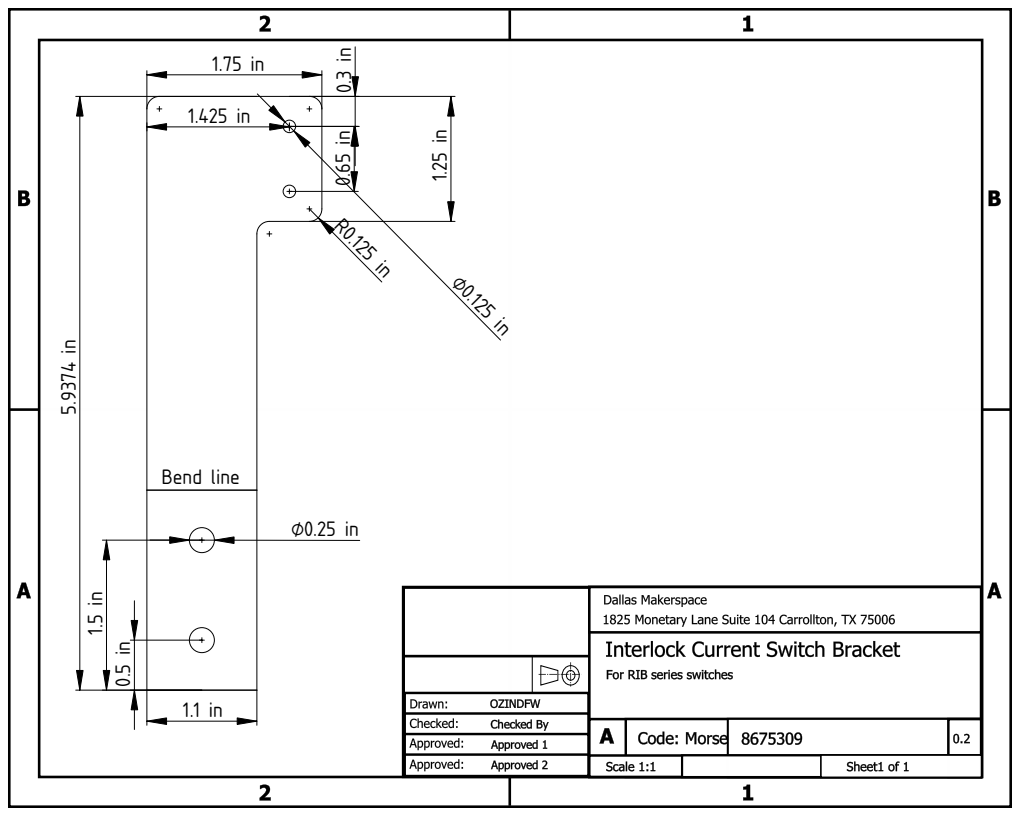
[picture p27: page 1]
Bend line

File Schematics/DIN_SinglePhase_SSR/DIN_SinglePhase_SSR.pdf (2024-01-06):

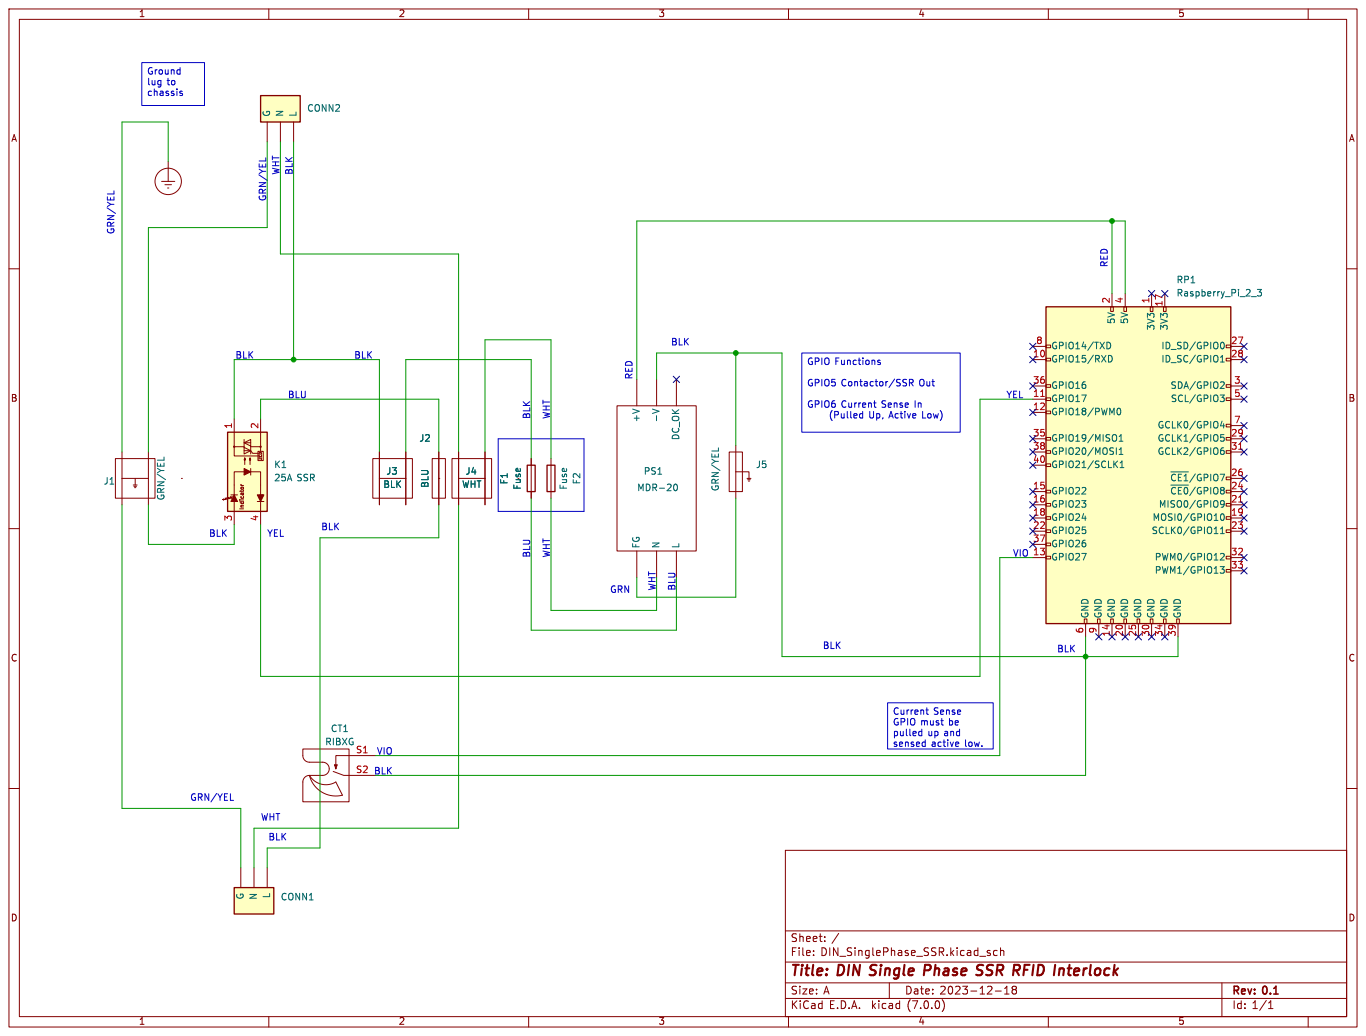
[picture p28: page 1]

Id: 1/1 Title: DIN Single Phase SSR RFID Interlock

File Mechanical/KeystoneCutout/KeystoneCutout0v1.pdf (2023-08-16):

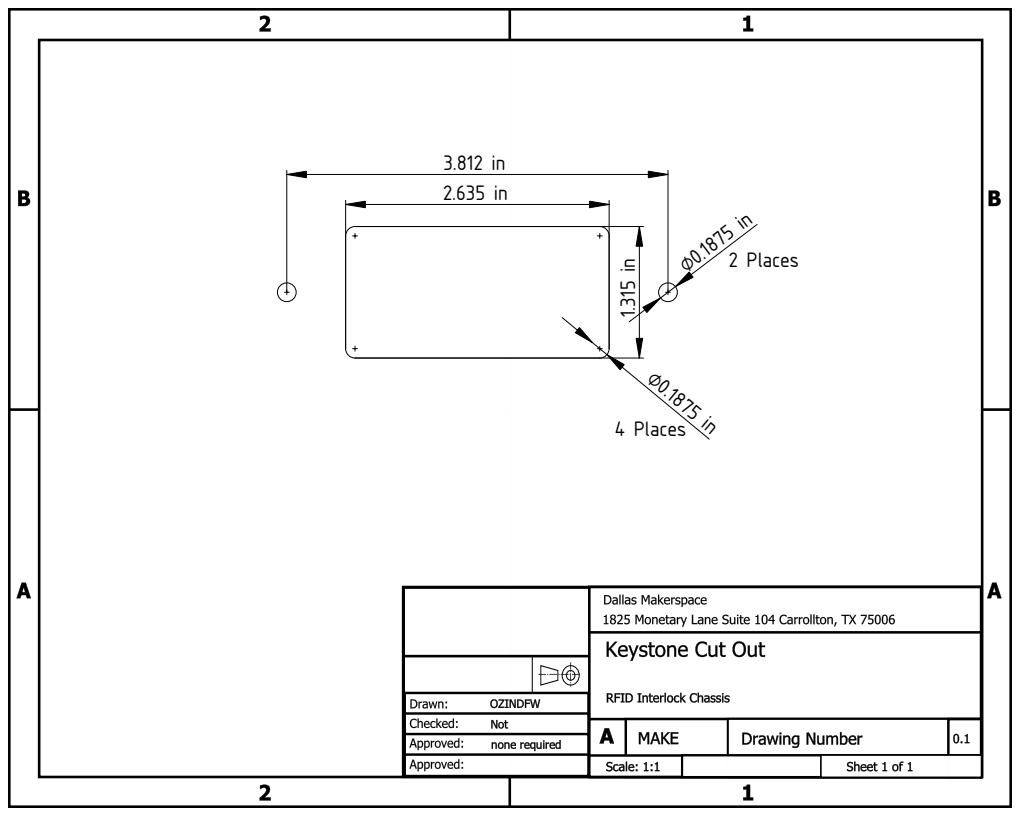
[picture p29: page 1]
Place

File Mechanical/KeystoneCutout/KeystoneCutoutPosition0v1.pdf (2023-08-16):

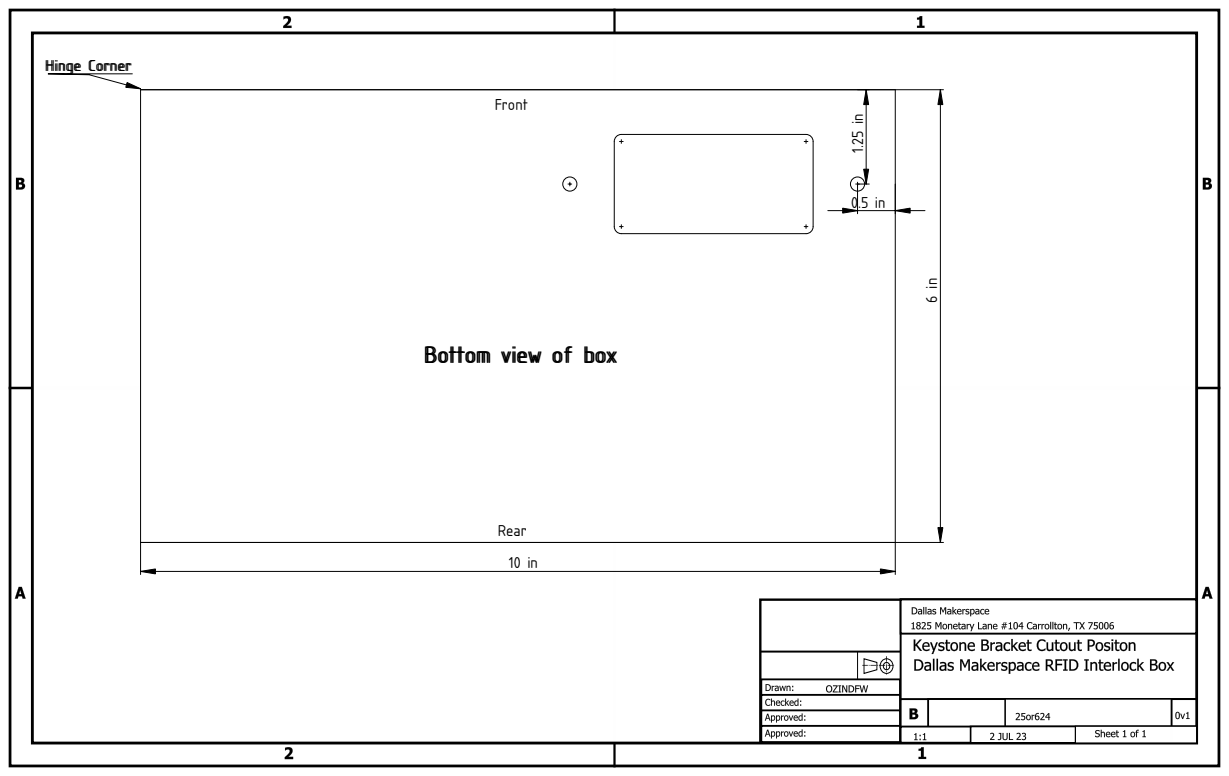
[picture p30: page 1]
Front; HHiinnggee CCoorrnneerr

BBoottttoomm vviieeww ooff bbooxx

Rear

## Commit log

2024-01-06 Initial upload
    [RFID_CurrentSense_Bracket_0v2.DXF, RFID_CurrentSense_Bracket_0v2.FCStd, RFID_CurrentSense_Bracket_Bare_0v2.FCStd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]
2024-01-28 Delete Mechanical/DIN_Baseplate/RFID_LO_DIN_Baseplate_0v2.FCStd
    revised to 0.2b
    [RFID_LO_DIN_Baseplate_0v2.FCStd]
2024-01-28 Delete Mechanical/DIN_Baseplate/RFID_LO_DIN_Baseplate_0v2a.FCStd
    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
    [RFID_LO_DIN_Baseplate_0v2a.FCStd]
2024-01-28 revised from 0.2a
    minor corrections and added annotations.
    [RFID_LO_DIN_Baseplate_0v2b.FCStd]
2024-01-28 Current sense bracket for 3D printing
    [RFID_CurrentSense_Bracket_3D_0v1b-Body.stl, RFID_CurrentSense_Bracket_3D_0v1b.FCStd]
2024-02-05 Update RFID_Install&Maint.md
    Addition of some tools and materials.
2024-08-05 Add files via upload
    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
    [Reader_Holder_0v1-BodyPad.stl, Reader_Holder_0v1.FCStd, Reader_Holder_0v1b-BodyFillet.stl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]
2024-09-07 correct indicator wiring
2024-09-07 Update RFID_Install&Maint.md
    Add comments about box modification for installation, indicator and emergency stop switch.
